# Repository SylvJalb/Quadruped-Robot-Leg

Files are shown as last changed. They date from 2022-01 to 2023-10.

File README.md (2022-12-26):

# Quadruped Robot (Only front right leg)
<p align="middle">
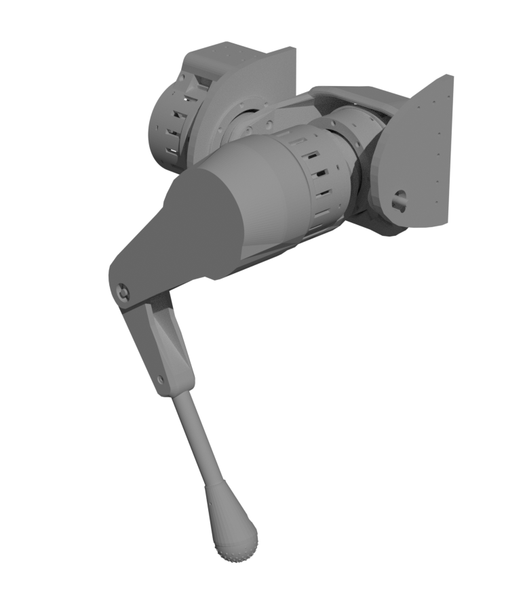
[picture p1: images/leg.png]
Design

Simulator Test
Real Test
</p>

## 🚨 Disclaimer
Please note: I have just started to learn how to use Blender.       
Any informative comment, or participation in the project is welcome ;)

## Software
I use Blender to design my project. You can import in your Blender the "leg.blend" file.

## Actuators
For the actuators I use the opensource OpenTorque Actuator project made by [Gabrael Levine](https://hackaday.io/project/159404-opentorque-actuator).
I use more particularly the redesigned OpenTorque Actuator, by the Youtuber [Skyentific](https://www.youtube.com/c/Skyentific), then redesigned again by [RevisonNr3](https://www.thingiverse.com/thing:5155183) / [acisre](https://discourse.odriverobotics.com/t/opentorque-project-new-design/8280).
Finals Actuators STL Files are in the folder "openTorqueFiles".

# What you will need
🚨 Warning ! These are the exact components I purchased for my prototype. All prices and links are from January 10, 2022 ... They may not be current anymore ! The prices are therefore only to give you an idea.     

| Piece | Number | Dimensions | Price ~ | Link (Exemple) |
|-----|:-----:|:-----:|:----:|:----:|
| Trapezoid toothed belts | 1 | 70c x 2cm | 20€ | [Amazon](https://www.amazon.fr/gp/product/B092PTVXP8/ref=ppx_yo_dt_b_asin_title_o00_s00?ie=UTF8&th=1) |
| Rubber ball | 1 | diameter: 6cm | 8€ | [Amazon](https://www.amazon.fr/gp/product/B00LSO64DY/ref=ppx_yo_dt_b_asin_title_o01_s00?ie=UTF8&th=1) |
| Steel cylinder | 3 | 8 x 100mm | 8€ | [Amazon](https://www.amazon.fr/gp/product/B081JNJPV2/ref=ppx_yo_dt_b_asin_title_o02_s00?ie=UTF8&psc=1) |
| Steel cylinder | 1 | 3 x 28mm | 1€ | [Amazon](https://www.amazon.fr/dp/B07MBNXDT3?psc=1&smid=A38WCF64ZZVDKC&ref_=chk_typ_imgToDp) |
| Ball bearing | 6 | 70 x 90 x 10mm | 57€ | [Aliexpress](https://fr.aliexpress.com/item/763194187.html?spm=a2g0o.9042311.0.0.2f326c37LDlLac) |
| Ball bearing | 18 | 15 x 28 x 7mm  | 20€ | [Aliexpress](https://fr.aliexpress.com/item/900706083.html?spm=a2g0o.9042311.0.0.2f326c37LDlLac) |
| Ball bearing | 4 | 8 x 22 x 7mm | 14€ | [Aliexpress](https://fr.aliexpress.com/item/4000984095586.html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) |
| Screw (flat head) | 12 | M4 x 10mm | 2€ | [Aliexpress](https://fr.aliexpress.com/item/1005003411992910.html?spm=a2g0o.9042311.0.0.2f326c37LDlLac) |
| Screw (flat head) | 42 | M3 x 20mm | 3€ | [Aliexpress](https://fr.aliexpress.com/item/4001072025844.html?spm=a2g0o.9042311.0.0.2f326c37LDlLac) |
| Screw (flat head) | 30 | M3 x 10mm | 3€ | [Aliexpress](https://fr.aliexpress.com/item/4001072025844.html?spm=a2g0o.9042311.0.0.2f326c37LDlLac) |
| Screw (socket head) | 12 | M4 x 20mm | 3€ | [Aliexpress](https://fr.aliexpress.com/item/1005001975621423.html?spm=a2g0o.9042311.0.0.2f326c37LDlLac) |
| Screw (socket head) | 57 | M3 x 20mm | 4€ | [Aliexpress](https://fr.aliexpress.com/item/1005001975621423.html?spm=a2g0o.9042311.0.0.2f326c37LDlLac) |
| Screw (socket head) | 12 | M2.5 x 10mm | 1.5€ | [Aliexpress](https://fr.aliexpress.com/item/1005001975621423.html?spm=a2g0o.9042311.0.0.2f326c37LDlLac) |
| Nut | 30 | M4 | 1.5€ | [Aliexpress](https://fr.aliexpress.com/item/32798773566.html?spm=a2g0o.9042311.0.0.2f326c37LDlLac) |
| Nut | 96 | M3 | 1.5€ | [Aliexpress](https://fr.aliexpress.com/item/32798773566.html?spm=a2g0o.9042311.0.0.2f326c37LDlLac) |
| Nut | 12 | M2.5 | 3€ | [Aliexpress](https://fr.aliexpress.com/item/32798773566.html?spm=a2g0o.9042311.0.0.2f326c37LDlLac) |
| Power supply | 1 | 1500W / 24V 62.5a | 80€ | [Aliexpress](https://fr.aliexpress.com/item/4000918005199.html?spm=a2g0o.9042311.0.0.2f326c37LDlLac) |
| Magnetic rotation encoder | 3 | 14-bit | 57€ | [Aliexpress](https://fr.aliexpress.com/item/1005001688635554.html?spm=a2g0o.9042311.0.0.2f326c37LDlLac) |
| Engine controler | 2 | 2 motors | 170€ | [Aliexpress](https://fr.aliexpress.com/item/1005002349959313.html?spm=a2g0o.9042311.0.0.2f326c37LDlLac) |
| Brushless motor | 3 | W9235 (X8318S) | 170€ | [Aliexpress](https://fr.aliexpress.com/item/4001103601935.html?spm=a2g0o.9042311.0.0.2f326c37LDlLac) |
| Cables |  | 2m | 1€ | [Aliexpress](https://fr.aliexpress.com/item/1005001876779326.html?spm=a2g0o.9042311.0.0.20926c37dbOLOt) |

**TOTAL : ~ 628 EUR** *(~ 720 USD)*   
***PLA, Nylon, and screws for the leg are missing in the table!***

So for around 630 € you can fully do this leg. If you want to do others, be aware that some components can be used for several legs ...
For 4 legs, I think it could cost 550 euros per leg. However this fast calcul does not include the price of the tools, the battery (for autonomous robot), and the raspberry pi (for example).

# TO DO LIST :
- [x] Import the Opentorque remaked project in my 3D plan.      
- [x] Design the leg in 3D.     
- [x] Make it printable with 3D printer.        
- [X] Print & Assemble motors.      
- [X] Test motors.      
- [X] Print & Assemble leg.     
- [X] Make a simple wood testing workbench.      
- [X] Test leg & Correct the latest mistakes.       
- [ ] Make the assembly manual (probably in yt videos).        
- [X] Develop sofware to move the leg (in Python)         
- [X] Redevelop the software to move the leg (in Rust) to have better calcul performance.       
- [X] Make a Python library from the Rust code. (to use it in developement/simulation environment)

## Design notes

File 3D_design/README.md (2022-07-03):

# Print informations

Brand: [Creality](https://www.creality3dofficial.com/)  
Model: [Ender 3 Pro](https://www.creality3dofficial.com/products/creality-ender-3-pro-3d-printer/)      
Filament size: 1.75mm       

## **Leg**
### > PLA
Use PLA Generic default settings in Cura, and change :
- Wall thickness: 4mm   
<!--- - Deactivate "Mesh Fixes" > "Union Overlapping Volumes" -->

| Part | Nozzle Size | Thickness | Infill | Support | Adhesion | Weight |
|:----|:---:|:---:|---:|:---:|:---:|---:|
| arm_case_lid | 0.8 | 0.32 | 50% | No | No | 54g |
| arm_case_part1 | 0.8 | 0.32 | 30% | 51° | No | 197g |
| arm_case_part2 | 0.8 | 0.32 | 50% | 51° | No | 192g |
| arm_holder | 0.8 | 0.32 | 50% | 51° | No | 304g |
| arm_separator | 0.8 | 0.32 | 40% | No | No | 30g |
| foot_holder_part1 | 0.4 | 0.2 | 50% | 35° | No | 23g |
| foot_holder_part2 | 0.4 | 0.2 | 50% | 35° | No | 22g |
| forearm_holder | 0.4 | 0.2 | 50% | 35° | No | 100g |
| forearm_gear_arm | 0.4 | 0.16 | 60% | No | No | 50g |
| forearm_gear_knee | 0.4 | 0.16 | 30% | No | No | 28g |
| forearm_separators (1&2) | 0.4 | 0.32 | 100% | No | No | 3g |
| shoulder_case | 0.8 | 0.32 | 50% | 51° | Yes | 564g |
| shoulder_holder_back | 0.8 | 0.32 | 30% | 51° | No | 282g |
| shoulder_holder_front | 0.8 | 0.32 | 30% | No | No | 107g |
| shoulder_separator | 0.8 | 0.32 | 40% | No | No | 30g |

### > TPU 95A
Use TPU 95A Generic default settings in Cura, and change :
- nozzle size: 0.4mm
- Layer height: 0.12mm
- Infill: 20%
- Infill pattern: Cubic Subdivision
- Infill line multiplier: 3
- Wall thickness: 1.5mm
- Printing temperature: 228°C
- Build plate temperature: None

foot_ball -> 31g

## **OpenTorque Actuator**
You have to print 3 actuators. The first one is the one that is connected to the shoulder. The second one is the one that is connected to the arm. The third one is the one that is connected to the forearm. There are all three the same.

**This is instructions to print only one actuator :**

### > PLA
Use PLA Generic default settings in Cura, and change :
- Wall thickness: 2.4mm
- nozzle size: 0.4mm
- Layer height: 0.28mm
- No Adhesion plate

| Part | Infill | Support | Weight |
|:-----|:---:|:---:|:---:|
| actuator_housing_2_acisre | 50% | 50° | 142g |
| backplate_acisre | 50% | No | 41g |
| encoder_cover_acisre | 20% | No | 11g |
| front_clamp_ring_acisre | 50% | No | 14g |
| magnet_holder | 30% | No | 2g |
| planet_carrier_2_acisre | 60% | 35° | 45g |
| planet_carrier_acisre | 100% | 35° | 68g |

### > Nylon
Use PLA Generic default settings in Cura, and change :
- nozzle size: 0.4mm
- Layer height: 0.2mm
- Wall thickness: 0.8mm
- Printing temperature: 260°C
- Build plate temperature: 70°C
- Printing speed: 35mm/s
- Retraction distance: 1.5mm
- Minimum extrusion distance window: 3mm
- No Adhesion plate
- Disable Print Cooling

| Part | Infill | Support | Weight for 1 | Quantity |
|:-----|:---:|:---:|:---:|:---:|
| actuator_housing_acisre | 70% | 60° | 110g | 1 |
| planet_gear_acisre | 70% | no | 12g | 3 |
| sun_gear_acisre | 60% | no | 15g | 1 |

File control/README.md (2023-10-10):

# Environements
- The **Production** code, developed in **Rust**, is in the `./src/` directory      
- The **Development** and **Simulation** code, developed in **Python**, is in the `./dev/` directory        
It use the production Leg class, built with [PyO3](https://github.com/PyO3/pyo3), to have a Python library thanks to [maturin](https://github.com/PyO3/maturin).     

# Rust Setup
Install Rust with [rustup](https://rustup.rs/).     

Install the cross-compilation toolchain for the raspberry pi:    
```bash
cargo install cross
```     

Build the project, here, like this:    
```bash
cargo build
```

# Python Setup
For this project I use python 3.10 in a virtual environement with `pyenv`.

## Setup python environment
First of all, create an run a virtual environment:    
```bash
pyenv virtualenv 3.10.0 robot
pyenv activate robot
```
Then, install the requirements:      
``` bash
pip install -r ./dev/requirements.txt
```
After that, you can create the python library with `maturin`:   
*(Rust code must be built before)*    
```bash
maturin develop
```
Now, you can run Python codes in the `dev` directory.
```bash
cd dev
python test.py
```

# Deploy on the robot (raspberry pi)
Install Cargo (on Linux and macOS systems)   
``` bash
curl https://sh.rustup.rs -sSf | sh
```

Build the rust code in your computer:
``` bash
docker build -t crossbuild:local .
cross build --target=armv7-unknown-linux-gnueabihf
```

Make sure you can do ssh connection with the raspberry pi and get the IP address of the raspberry pi.   

Copy the binary file `./target/armv7-unknown-linux-gnueabihf/debug/leg_controller` and the parameters file `params.json` to the raspberry pi with the `scp` command.     
``` bash
scp ./target/armv7-unknown-linux-gnueabihf/debug/leg_controller user@raspberrypi.local:leg_controller
scp ./params.json user@raspberrypi.local:params.json
```

# Upgrade th firmware of an ODrive 3.6 controller

1. Download your firmware from the [ODrive website](https://docs.odriverobotics.com/releases/firmware) or from the [ODrive Github](https://github.com/odriverobotics/ODrive/releases).

2. Convert the firmware to a binary file:
``` bash
sudo apt install binutils-arm-none-eabi
arm-none-eabi-objcopy -O binary file.elf file.bin
```
3. Switch to the `DFU` mode. (With the little switch on the ODrive board, near the USB port)

4. Install the `dfu-util` tool:
``` bash
sudo apt install dfu-util
```

5. Plug the ODrive to the computer, with USB cable. But don't power the ODrive with the power supply.

6. Flash the firmware:
``` bash
dfu-util -v -w -R -a 0 -d 0483:df11 -s 0x08000000:leave -D file.bin
```

7. Switch on the ODrive power supply.   
Wait for the firmware to be flashed.

8. At the end, turn off the ODrive power supply and switch back to the `RUN` mode.

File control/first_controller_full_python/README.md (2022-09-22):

# Setup
For this project i use python 3.10

## Odrive Installation
On terminal :       
``` bash
sudo pip3 install --upgrade odrive
```

## Setup python environment
Run a virtual environment and install the requirements      
``` bash
pip3 install -r requirements.txt
```

## Setup env
Create a new file named `env.py` and put your informations :        
``` python
# ODRIVE 1 is connected to the arm and forearm
ODRIVE_1_SN = "XXXXXXXXXXXX" # converted in Hexadecimal

# ODRIVE 2 is connected to the shoulder
ODRIVE_2_SN = "XXXXXXXXXXXX" # converted in Hexadecimal

# The MODE to run the program
MODE = "motor" # "simulation" or "motor"
```

## Run the test program 
This test program run the following instructions :      
- Detect ODRIVE Cards
- Setup with parameters
- Run the calibration (This may take some time...)
- Run the walking loop

On your raspberry pi, run the test program :
``` bash
cd ./tests
python3.10 ./test_leg_class.py
```

If the calibration fail, disconnect and reconnect the cards from current, retry to run the program.

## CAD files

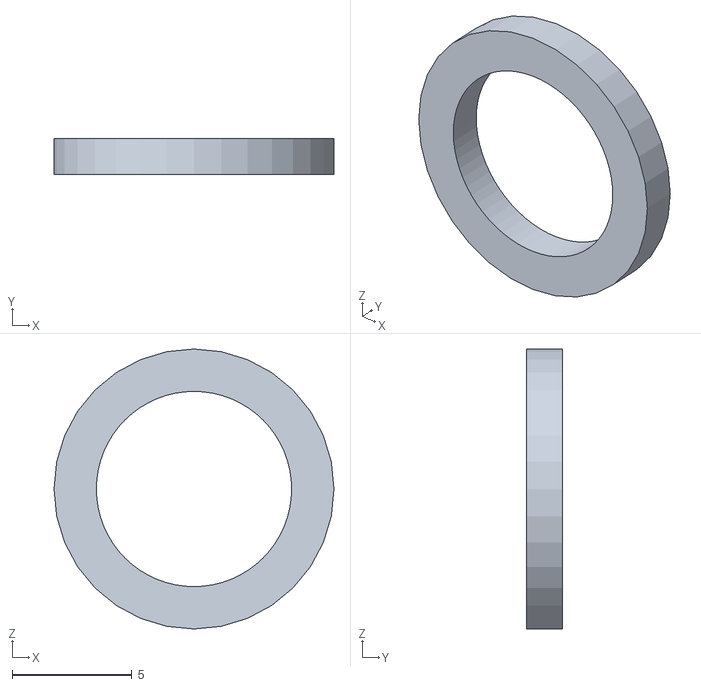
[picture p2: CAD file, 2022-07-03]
3D_design/leg/forearm_separator_part2.stl
11.7 x 1.50 x 11.7

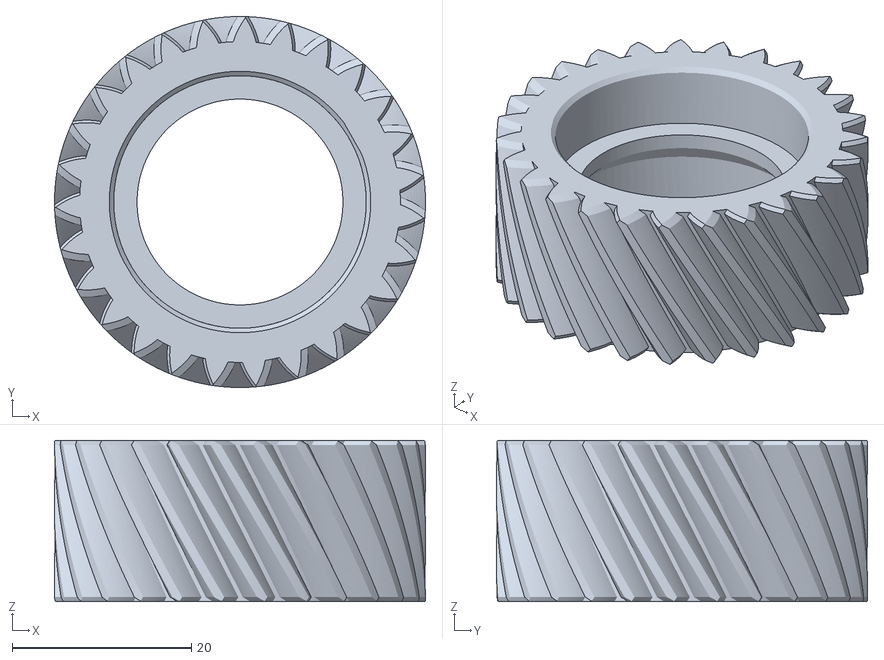
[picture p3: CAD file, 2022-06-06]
3D_design/openTorque/planet_gear_acisre.stl
41.4 x 41.4 x 18.0

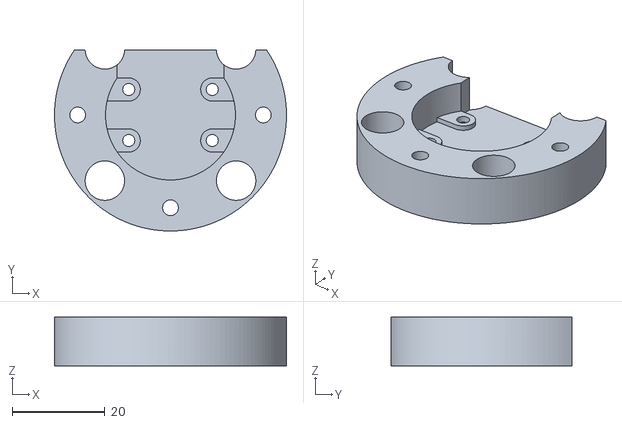
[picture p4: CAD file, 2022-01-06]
3D_design/openTorque/encoder_cover_acisre.stl
50.0 x 39.0 x 10.5

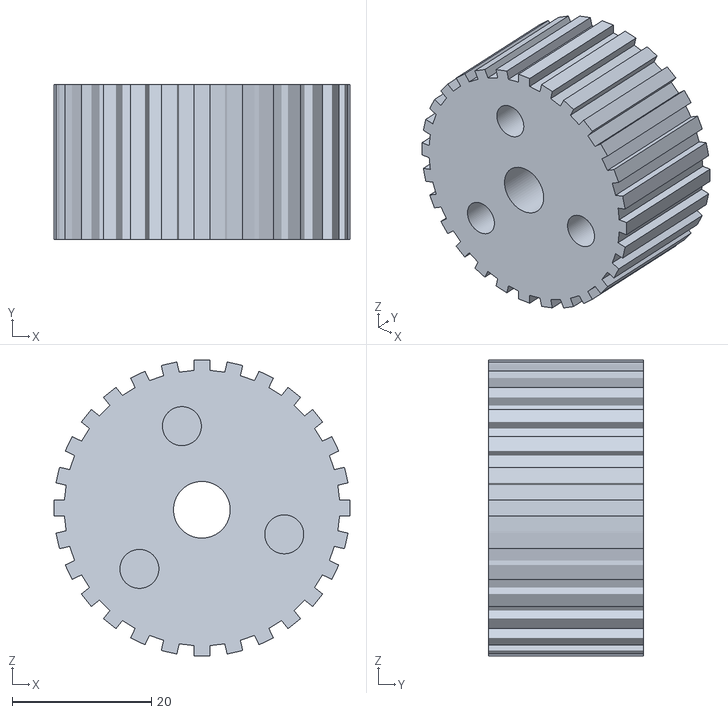
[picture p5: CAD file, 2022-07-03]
3D_design/leg/forearm_gear_knee.stl
42.5 x 22.3 x 42.5

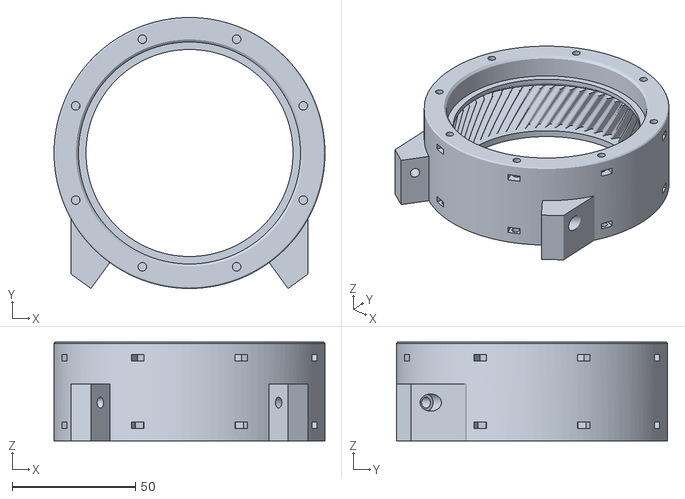
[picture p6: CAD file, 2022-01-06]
3D_design/openTorque/actuator_housing_acisre.stl
110.0 x 110.0 x 40.0

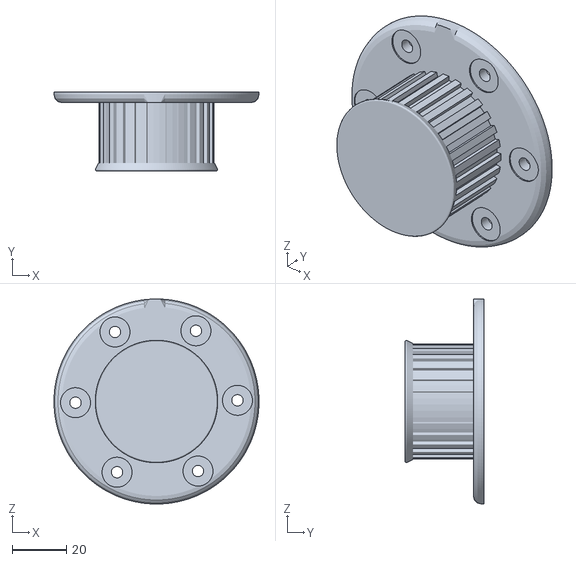
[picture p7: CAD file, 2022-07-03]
3D_design/leg/forearm_gear_arm.stl
75.9 x 29.1 x 75.9

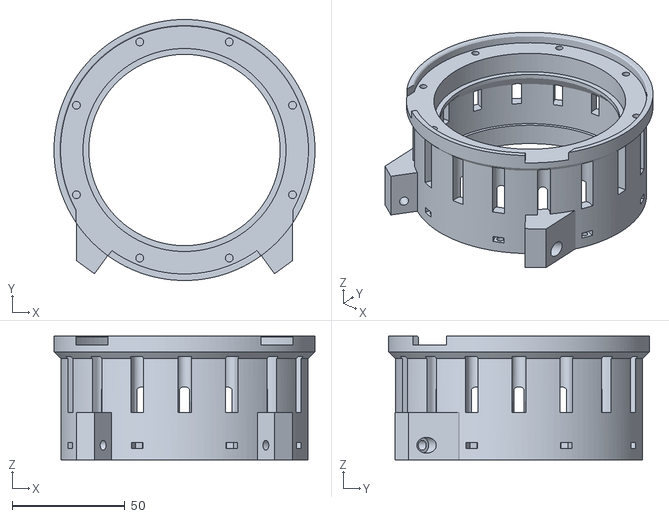
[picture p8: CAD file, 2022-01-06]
3D_design/openTorque/actuator_housing_2_acisre.stl
116.0 x 116.0 x 55.0

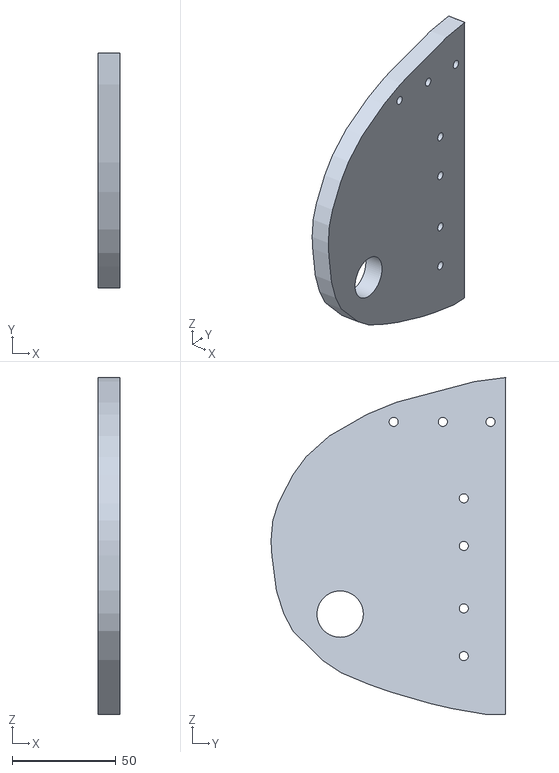
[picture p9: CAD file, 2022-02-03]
3D_design/leg/shoulder_holder_front.stl
10.5 x 113.4 x 162.6

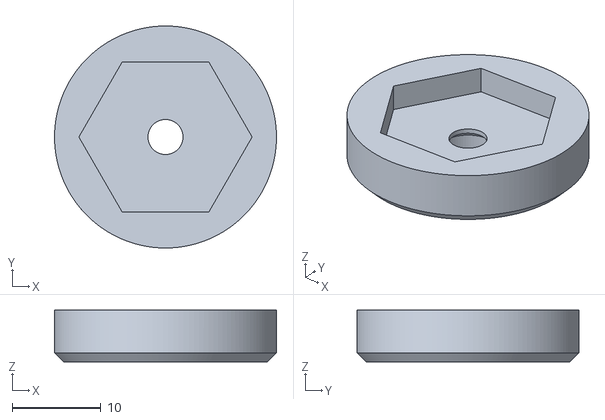
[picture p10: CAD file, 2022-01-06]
3D_design/openTorque/magnet_holder.stl
25.0 x 25.0 x 5.80

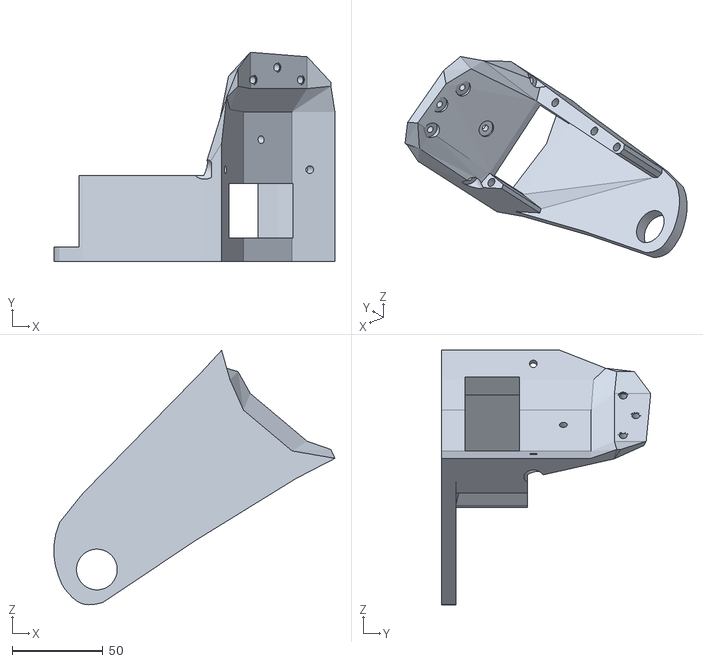
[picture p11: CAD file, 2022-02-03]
3D_design/leg/arm_case_part2.stl
154.4 x 115.1 x 139.9

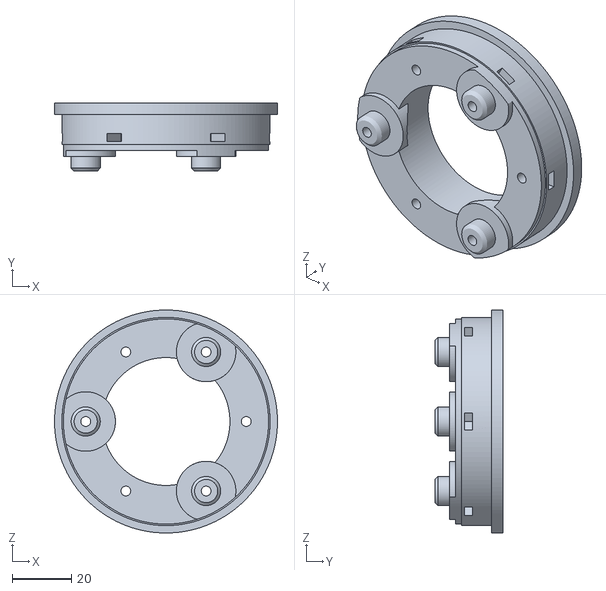
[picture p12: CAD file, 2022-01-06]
3D_design/openTorque/planet_carrier_2_acisre.stl
75.0 x 23.0 x 75.0

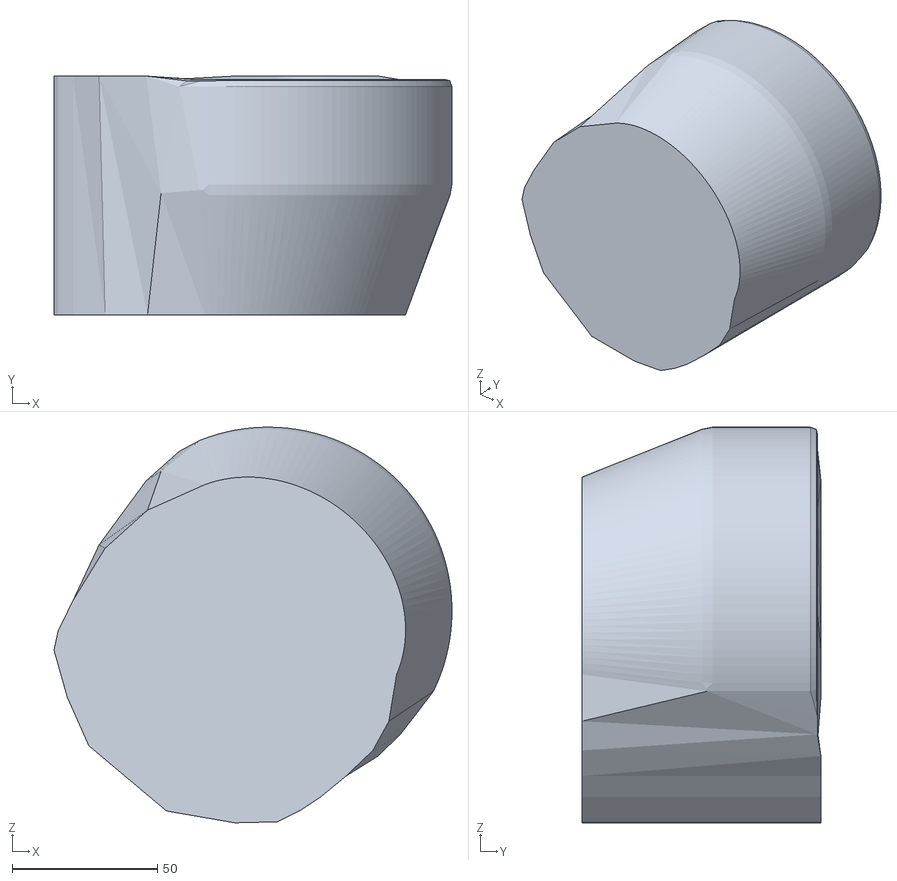
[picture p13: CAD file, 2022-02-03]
3D_design/leg/arm_case_part1.stl
136.9 x 82.2 x 136.1

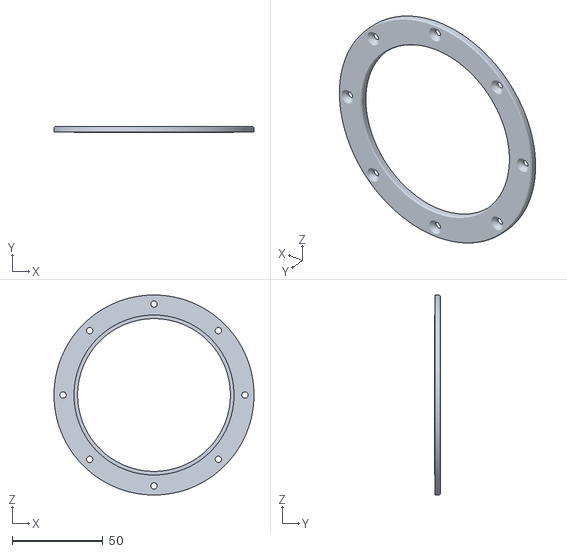
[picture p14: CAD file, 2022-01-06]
3D_design/openTorque/front_clamp_ring_acisre.stl
110.0 x 3.20 x 110.0

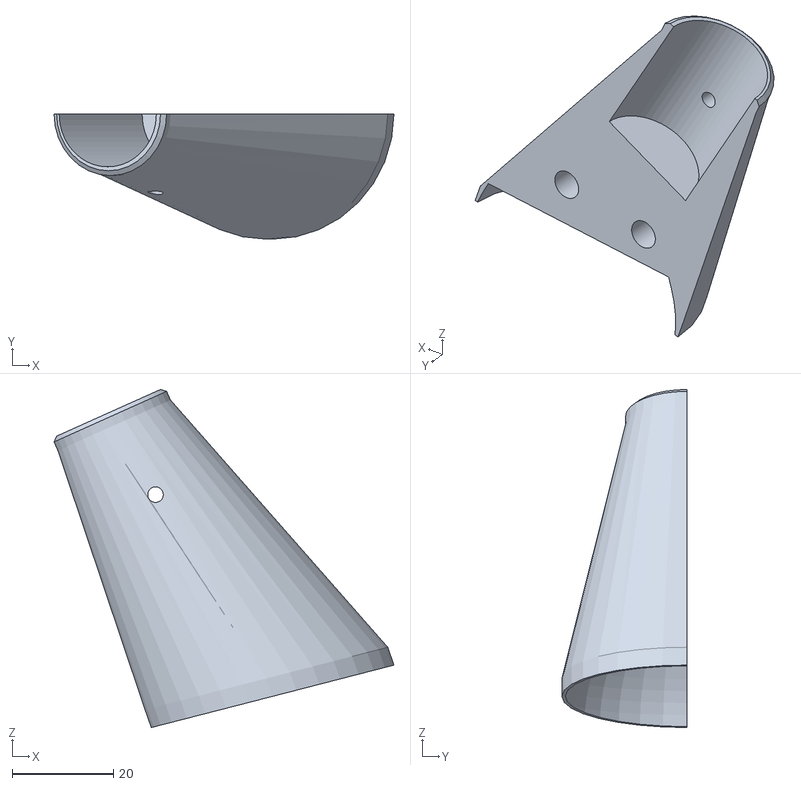
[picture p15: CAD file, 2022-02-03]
3D_design/leg/foot_holder_part1.stl
67.1 x 24.8 x 66.8

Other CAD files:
3D_design/leg/forearm_separator_part1.stl
3D_design/openTorque/sun_gear_acisre.stl
3D_design/leg/foot_holder_part2.stl
3D_design/openTorque/planet_carrier_acisre.stl
3D_design/leg/arm_case_lid.stl
3D_design/leg/arm_holder.stl
3D_design/leg/arm_separator.stl
3D_design/leg/forearm_holder.stl
3D_design/leg/shoulder_case.stl
3D_design/leg/shoulder_holder_back.stl
3D_design/leg/shoulder_separator.stl
3D_design/openTorque/backplate_acisre.stl

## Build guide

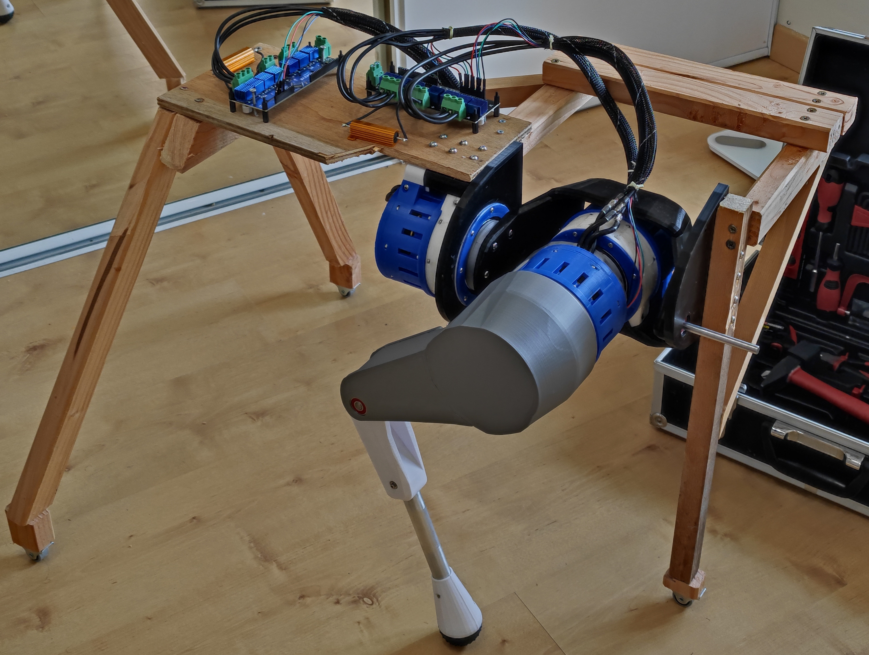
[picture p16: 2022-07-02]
images/leg_assembled.jpg

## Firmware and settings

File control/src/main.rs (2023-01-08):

use nalgebra::Vector3;

mod robot_module;
use robot_module::RobotModule;

fn main() {
    // create a new Leg instance
    let mut my_robot = RobotModule::new(Vector3::new(125.0, 50.0, -320.0));
    println!("{:?}", my_robot.get_leg());

    // init the robot
    my_robot.init_robot().expect("Error during robot initialization");

    // RUN A SIMPLE TEST
    loop {
        for number in -50..50 {
            my_robot.set_foot_position(&Vector3::new(125.0, number as f32, -320.0))
                .expect("Error setting foot position");
            println!("{:?}", my_robot.get_leg());
        }
        for number in (-50..50).rev() {
            my_robot.set_foot_position(&Vector3::new(125.0, number as f32, -320.0))
                .expect("Error setting foot position");
            println!("{:?}", my_robot.get_leg());
        }
    }
}

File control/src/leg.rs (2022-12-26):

use std::fmt::Debug;
use std::fmt::Formatter;
use std::fs::File;
use std::io::{BufReader, Error, ErrorKind};
use std::f32::consts::PI;
use nalgebra::{Vector3, Rotation3};
use odrive_rs::enumerations::AxisID;

pub struct Leg {
        foot_pos: Vector3<f32>,
        odrives_ready: bool,
        shoulder: AxisID,
        arm: AxisID,
        forearm: AxisID,
        shoulder_pos: Vector3<f32>,
        arm_pos: Vector3<f32>,
        forearm_pos: Vector3<f32>,
        shoulder_angle: f32,
        arm_angle: f32,
        forearm_angle: f32,
        arm_vertical_pos: Vector3<f32>,
        forearm_vertical_pos: Vector3<f32>,
        foot_vertical_pos: Vector3<f32>,
        params: serde_json::Value
}


impl Debug for Leg {
        fn fmt(&self, f: &mut Formatter) -> Result<(), std::fmt::Error> {
                write!(f, "Leg {{\n\tfoot_pos:\t{:?} \n\n\tforearm_pos:\t{:?} \n\tforearm_angle:\t{:?} \n\n\tarm_pos:\t{:?} \n\tarm_angle:\t{:?} \n\n\tshoulder_pos:\t{:?} \n\tshoulder_angle:\t{:?} \n}}", self.foot_pos, self.forearm_pos, self.forearm_angle, self.arm_pos, self.arm_angle, self.shoulder_pos, self.shoulder_angle)
        }
}

impl Leg {
        /*
        Initialize the leg
        foot_position : position of foot
        */
        pub fn new(foot_position: Vector3<f32>) -> Self {
                let mut new_leg = Leg {
                        foot_pos: foot_position,
                        odrives_ready: false,
                        shoulder: AxisID::Zero,
                        arm: AxisID::Zero,
                        forearm: AxisID::Zero,
                        shoulder_pos: Vector3::zeros(),
                        arm_pos: Vector3::zeros(),
                        forearm_pos: Vector3::zeros(),
                        shoulder_angle: 0.0,
                        arm_angle: 0.0,
                        forearm_angle: 0.0,
                        arm_vertical_pos: Vector3::zeros(),
                        foot_vertical_pos: Vector3::zeros(),
                        forearm_vertical_pos: Vector3::zeros(),
                        params: serde_json::Value::Null
                };


                // read params json file located "./params.json"
                let file = File::open("./params.json").expect("file should open read only");
                let reader = BufReader::new(file);
                new_leg.params = serde_json::from_reader(reader).expect("file should be proper JSON");

                match new_leg.update_positions() {
                        Ok(_) => (),
                        Err(e) => println!("Error: {:?}", e)
                }

                if new_leg.params.get("MODE").unwrap() == "motor" {
                        // TO DO: find and setup odrives cards
                        println!("Odrives not yet implemented");
                } else {
                        println!("Simulation mode");
                        new_leg.odrives_ready = false;
                }
                return new_leg;
        }

        /*
        Calibrate the leg
        */
        pub fn calibrate(&self) -> Result<(), Error> {
                /*
                if self.odrives_ready {
                        println!("Calibrating :");

                        // Calibrate shoulder
                        println!("	shoulder...  ");
                        let mut attempt = 1;
                        while !self.shoulder.motor.is_calibrated {
                                println!("		status : {:?} ", self.shoulder.motor.is_calibrated);
                                if attempt > 3 {
                                        return Err(Error::new(ErrorKind::Other, "Calibration failed on shoulder"));
                                }
                                run_calibration(self.shoulder);
                                attempt += 1;
                                sleep(10);
                        }
                        sleep(5);
                        println!("		status : {:?} ", self.shoulder.motor.is_calibrated);
                        
                        // Calibrate arm
                        println!("	arm...  ");
                        attempt = 1;
                        while !self.arm.motor.is_calibrated {
                                println!("		status : {:?} ", self.arm.motor.is_calibrated);
                                if attempt > 3 {
                                        return Err(Error::new(ErrorKind::Other, "Calibration failed on arm"));
                                }
                                run_calibration(self.arm);
                                attempt += 1;
                                sleep(10);
                        }
                        sleep(5);
                        println!("		status : {:?} ", self.arm.motor.is_calibrated);
                        
                        // Calibrate forearm
                        println!("	forearm...");
                        attempt = 1;
                        while !self.forearm.motor.is_calibrated {
                                println!("		status : {:?} ", self.forearm.motor.is_calibrated);
                                if attempt > 3 {
                                        return Err(Error::new(ErrorKind::Other, "Calibration failed on forearm"));
                                }
                                run_calibration(self.forearm);
                                attempt += 1;
                                sleep(10);
                        }
                        sleep(5);
                        println!("		status : {:?} ", self.forearm.motor.is_calibrated);
                        
                        println!("Calibration done !");

                        blocked_motor_mode(self.shoulder);
                        blocked_motor_mode(self.arm);
                        blocked_motor_mode(self.forearm);
                        println!("Motors blocked !");
                } else {
                        return Err(Error::new(ErrorKind::Other, "ODrives not Ready"));
                }
                */
                return Ok(());
        }
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

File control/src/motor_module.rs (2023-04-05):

use std::f32::consts::PI;
use std::path::Path;
use std::io::{BufReader, Error};
use std::fs::File;
use std::fmt::{Debug, Formatter};
use serialport::{SerialPortSettings, posix::TTYPort};

mod odrive;
pub use odrive::commands::{ODrive};
pub use odrive::enumerations::{AxisState, AxisID, ControlMode};

pub struct MotorModule {
    name: String,
    axis_id: AxisID,
    odrive: ODrive<TTYPort>,
    odrive_ready: bool,
    params: serde_json::Value,
}

impl Debug for MotorModule {
    fn fmt(&self, f: &mut Formatter) -> Result<(), std::fmt::Error> {
            write!(f, "Motor {{\n\tname:\t{:?} \n\taxis_id:\t{:?} \n\todrive:\t{:?} \n\todrive_ready:\t{:?} \n}}", self.name, self.axis_id, self.odrive, self.odrive_ready)
    }
}

impl MotorModule {
    pub fn new(name: String, axis_id: AxisID)-> Result<MotorModule, Error> {
        let file = File::open("./params.json").expect("file should open read only");
        let reader = BufReader::new(file);
        let params: serde_json::Value = serde_json::from_reader(reader).expect("file should be proper JSON");

        // Create serial port settings
        let mut settings = SerialPortSettings::default();
        // ODrive uses 115200 baud
        settings.baud_rate = 115_200;
        // Create serial port
        let serial = TTYPort::open(Path::new(params.get("PATHS").unwrap().get(name.to_ascii_uppercase() + "_USB").unwrap().as_str().unwrap()), &settings).expect("Failed to open usb port");
        // Create and return ODrive
        let odrive = ODrive::new(serial);

        Ok(MotorModule {
            name: name,
            axis_id: axis_id,
            odrive: odrive,
            odrive_ready: false,
            params: params,
        })
    }

    // Configure the motor
    // Use the params.json file to set the motor properties
    pub fn configure(&mut self)-> Result<(), Error> {
        println!("{}", self.odrive.get_config_property("encoder.config.cpr").unwrap().to_string());
        self.odrive.set_axis_property(self.axis_id, "controller.config.vel_limit", self.params.get("MOTORS").unwrap().get("VEL_LIMIT").unwrap()).unwrap();
        self.odrive.set_axis_property(self.axis_id, "encoder.config.cpr", self.params.get("MOTORS").unwrap().get("CPR").unwrap()).unwrap();
        self.odrive.set_axis_property(self.axis_id, "motor.config.pole_pairs", self.params.get("MOTORS").unwrap().get("POLE_PAIRS").unwrap()).unwrap();
        self.odrive.set_axis_property(self.axis_id, "motor.config.current_lim", self.params.get("MOTORS").unwrap().get("CURRENT_LIM").unwrap()).unwrap();
        self.odrive.set_axis_property(self.axis_id, "motor.config.calibration_current", self.params.get("MOTORS").unwrap().get("CURRENT_LIM").unwrap()).unwrap();
        self.odrive.set_axis_property(self.axis_id, "motor.config.resistance_calib_max_voltage", self.params.get("MOTORS").unwrap().get("CALIB_VOLTAGE_LIM").unwrap()).unwrap();
        self.odrive.set_axis_property(self.axis_id, "motor.config.torque_constant", self.params.get("MOTORS").unwrap().get("TORQUE_CONSTANT").unwrap()).unwrap();
        self.odrive.set_axis_property(self.axis_id, "config.startup_motor_calibration", false).unwrap();
        self.odrive.set_axis_property(self.axis_id, "config.startup_encoder_index_search", false).unwrap();
        self.odrive.set_axis_property(self.axis_id, "config.startup_encoder_offset_calibration", false).unwrap();
        self.odrive.set_axis_property(self.axis_id, "config.startup_closed_loop_control", false).unwrap();
        self.odrive.set_axis_property(self.axis_id, "config.startup_sensorless_control", false).unwrap();
        self.odrive.set_axis_property(self.axis_id, "encoder.config.use_index", false).unwrap();

        
        self.odrive.set_control_mode(self.axis_id, ControlMode::PositionControl).unwrap();
    
        self.odrive.save_configuration().unwrap();
        Ok(())
    }
    
    // Run the motor calibration routine
    pub fn calibrate(&mut self)-> Result<(), Error> {
        // Calibrate ODrive
        self.odrive.run_state(self.axis_id, AxisState::MotorCalibration, true).unwrap();
        // set motor pre calibrated
        self.odrive.set_motor_pre_calibrated(self.axis_id, true).unwrap();
        self.odrive.run_state(self.axis_id, AxisState::EncoderOffsetCalibration, true).unwrap();
        self.odrive.set_encoder_pre_calibrated(self.axis_id, true).unwrap();
        self.odrive.save_configuration().unwrap();
        Ok(())
    }

    // Arm the motor to be ready to move
    pub fn arm(&mut self)-> Result<(), Error> {
        // Arm ODrive
        self.odrive.run_state(self.axis_id, AxisState::ClosedLoopControl, false).unwrap();
        self.odrive_ready = true;
        Ok(())
    }

    // Set the motor position and velocity
    // Position is given in degrees
    pub fn set_position_and_velocity(&mut self, position: f32, velocity: f32)-> Result<(), Error> {
        // Set position and velocity
        // Position is in degrees, so convert to radians
        self.odrive.set_position_p(self.axis_id, position * PI / 180.0, Some(velocity), None).unwrap();
        Ok(())
    }

    pub fn is_ready(&self)-> bool {
        self.odrive_ready
    }
}

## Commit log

2022-01-06 add 3 opentorques in 3d model
    [actuator_housing_2_acisre.stl, actuator_housing_acisre.stl, backplate_acisre.stl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]
2022-01-07 Update README
    add Gabrael Levine (OpenTorque Actuator) link
2022-01-08 Arm case/holder in place
2022-01-08 first arm 3D version
2022-01-10 Make some parts printable
2022-01-10 Add some 3D holes for the screws
2022-01-11 remove material to reduce weight
2022-01-11 add holes for some screws
2022-01-11 Add more 3D holes for the screws
2022-01-11 Export 3D printable files
    [actuator_housing_2_acisre.stl, actuator_housing_acisre.stl, backplate_acisre.stl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]
2022-01-11 Separate OpenTorques in 3D blender file
    [leg_arm_axe.stl, leg_arm_case_lid.stl, leg_arm_case_part1.stl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]
2022-01-12 slim some parts
    [leg_arm_axe_back.stl, leg_arm_case_lid.stl, leg_arm_case_part1.stl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]
2022-01-12 regenerate full leg STL file
2022-01-13 rename some files
    [actuator_housing_2_acisre.stl, actuator_housing_acisre.stl, arm_case_lid.stl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]
2022-01-13 3D print forearm_holder
    [forearm_holder.stl]
2022-01-13 some new prints updates
    [foot_holder_part1.stl, foot_holder_part2.stl]
2022-01-14 slim down some part
    [arm_holder.stl, shoulder_case.stl]
2022-01-14 UPDATE print informations
2022-01-14 New print informations
2022-01-16 update parts after some print test
    [arm_case_lid.stl, arm_case_part1.stl, arm_case_part2.stl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]
2022-01-18 Update OpenTorque Actuator Print Informations
    [stand.stl]
2022-01-20 reduce width of shoulder
    [arm_holder.stl, forearm_gear_arm.stl, forearm_gear_knee.stl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]
2022-01-22 update 3d print instructions
2022-01-27 update prints file
    [foot_holder_part1.stl, foot_holder_part2.stl, forearm_gear_arm.stl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]
2022-02-01 Start to redesign te arm shape
2022-02-02 add new arms holes for screws
2022-02-02 some print params update
    [shoulder_case.stl]
2022-02-02 corrections on the new arm design
2022-02-03 somes printing infos updates
    [arm_case_lid.stl, arm_case_part1.stl, arm_case_part2.stl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]
2022-02-05 new 3D print informations
    [forearm_separator_part1.stl, forearm_separator_part2.stl]
2022-06-06 some tests & resumption of project ;)
    [planet_gear_acisre.stl]
2022-07-02 update TO DO LIST - Assemble leg done
2022-07-02 new 3D design folder, with news gears for the forearm
    [actuator_housing_2_acisre.stl, actuator_housing_acisre.stl, arm_case_lid.stl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]
2022-07-02 forearm_gear_arm printing info update
2022-07-03 update forearm gear design to fit with belt
    [forearm_gear_arm.stl, forearm_gear_knee.stl, forearm_separator_part1.stl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]
2022-07-05 first test of leg -> everything seems to work !!!
2022-07-11 initialize leg python class file
2022-07-11 new motor class
2022-07-11 calcul arm position of the leg software
2022-07-12 calcul_forearm_position of software leg class
2022-07-12 new visualisation of the leg software class
2022-07-13 first tested version of the leg software class
2022-07-13 dynamic test of leg class
2022-08-11 best print of the leg software
2022-08-12 odrive usage in leg class
2022-08-16 better calibration process
2022-08-16 arm angle calcul correction
2022-08-16 remove motor position forcing ajustement after test series
2022-09-15 finalizing the leg class test code - THE LEG CAN WALK !
2022-11-08 first rust implementation (with bug and without odrive car usage)
    [leg.rs, main.rs]
2022-11-08 some errors corrections in the rust code
    [leg.rs]
2022-11-08 bug corrections in the rust code
    [leg.rs]
2022-12-25 correction in the implementation of the rust code in the python dev/test code
    [leg.rs]
2022-12-26 first simulation leg in panda3d
2022-12-26 corrections of the shoulder angle and flat_position in the leg calculator
    [leg.rs]
2022-12-26 last bug correction for test the simulator. It's work !
    [leg.rs]
2023-01-06 refactor python comunication with odrive, fully in rust
2023-01-07 convert degree rotation to randian and set the odrives USB paths in the parameter file
2023-04-05 motors calibrations from parameters
2023-10-10 Tuto to Upgrade the Firmware of an ODrive 3.6 controller
